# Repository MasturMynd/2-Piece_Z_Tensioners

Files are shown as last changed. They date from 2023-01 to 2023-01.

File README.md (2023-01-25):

# 2-Piece Z Tensioners

Frustrated by a number of cracked stock Z tensioners, I finally decided to take matters into my own hands. The print orientation of the stock Z tensioners puts the most force along the layer lines which can easily result in delamination under normal use. These 2-piece tensioners change the print orientation so the forces being applied are perpendicular to the layer lines, resulting in a stronger part.

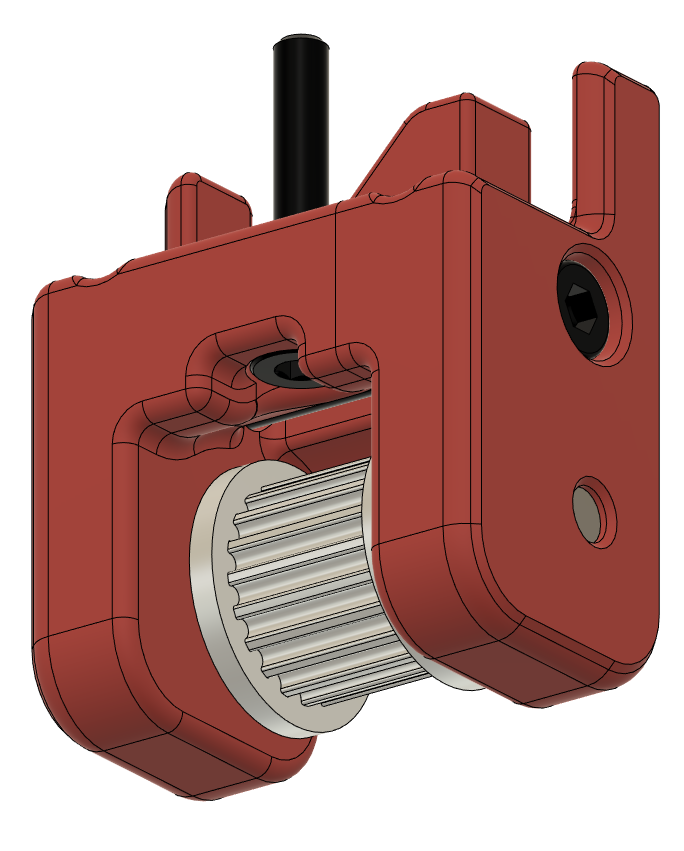
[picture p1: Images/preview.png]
Preview


BOM
---
| Category | Part Description | Qty | Notes |
| --- | --- | --- | --- |
| | M3x25 BHCS | 4 | |
| | M3 Brass heatstake inserts - short M3x5x4 | 4 | |

# Assembly

Before We Begin
---
Make sure that you have the proper parts printed for your setup. If you're using the BOM hardware (M5x30 BHCS) make sure you don't have the internal flange.
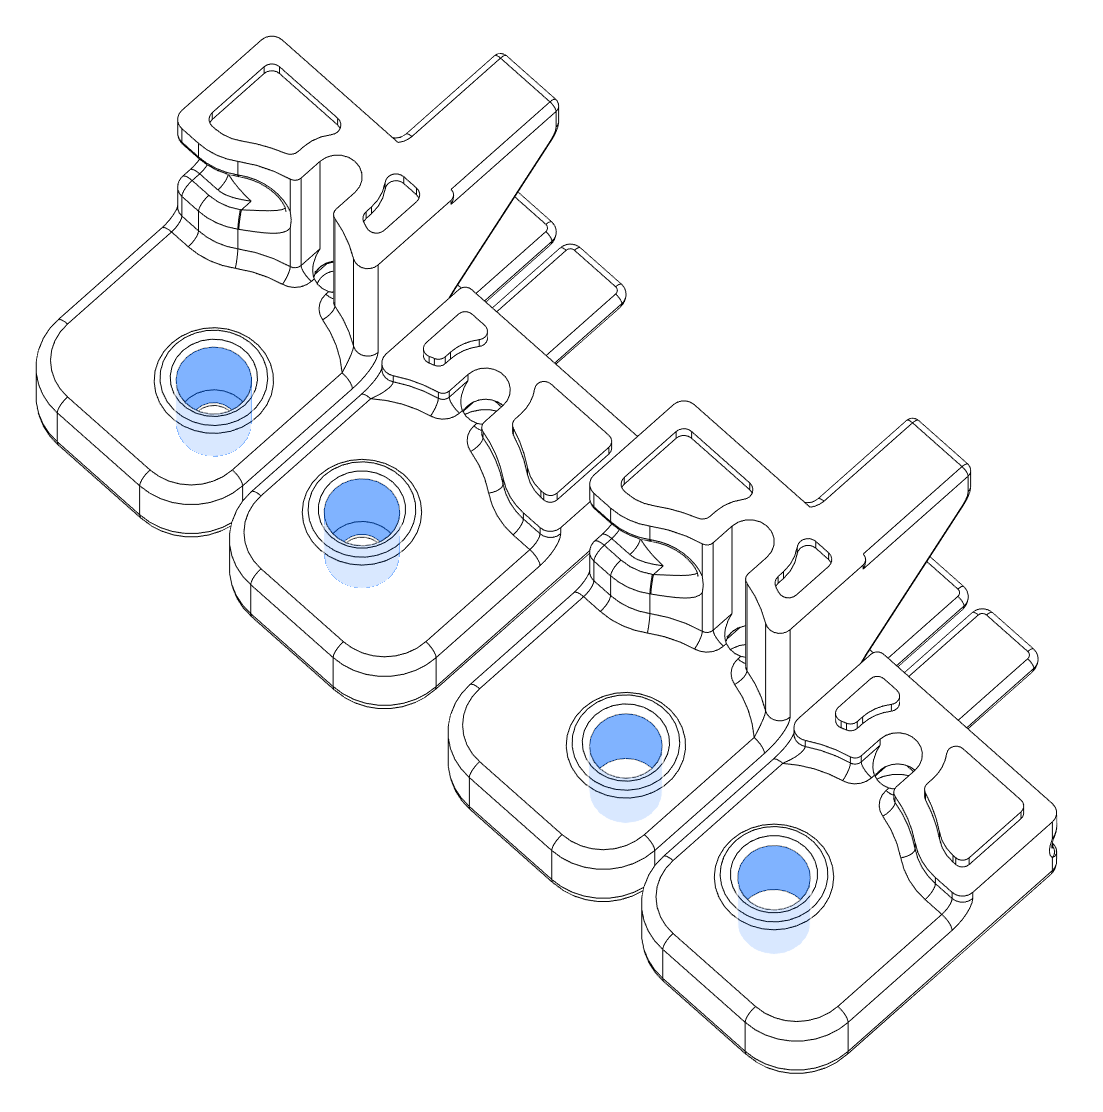
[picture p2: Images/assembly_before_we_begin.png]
Assembly_Before_We_Begin


Heatset Insert
---
Each tensioner assembly requires a single heatset insert that will be used in combination with an M3x25 SHCS to clamp the two pieces together.
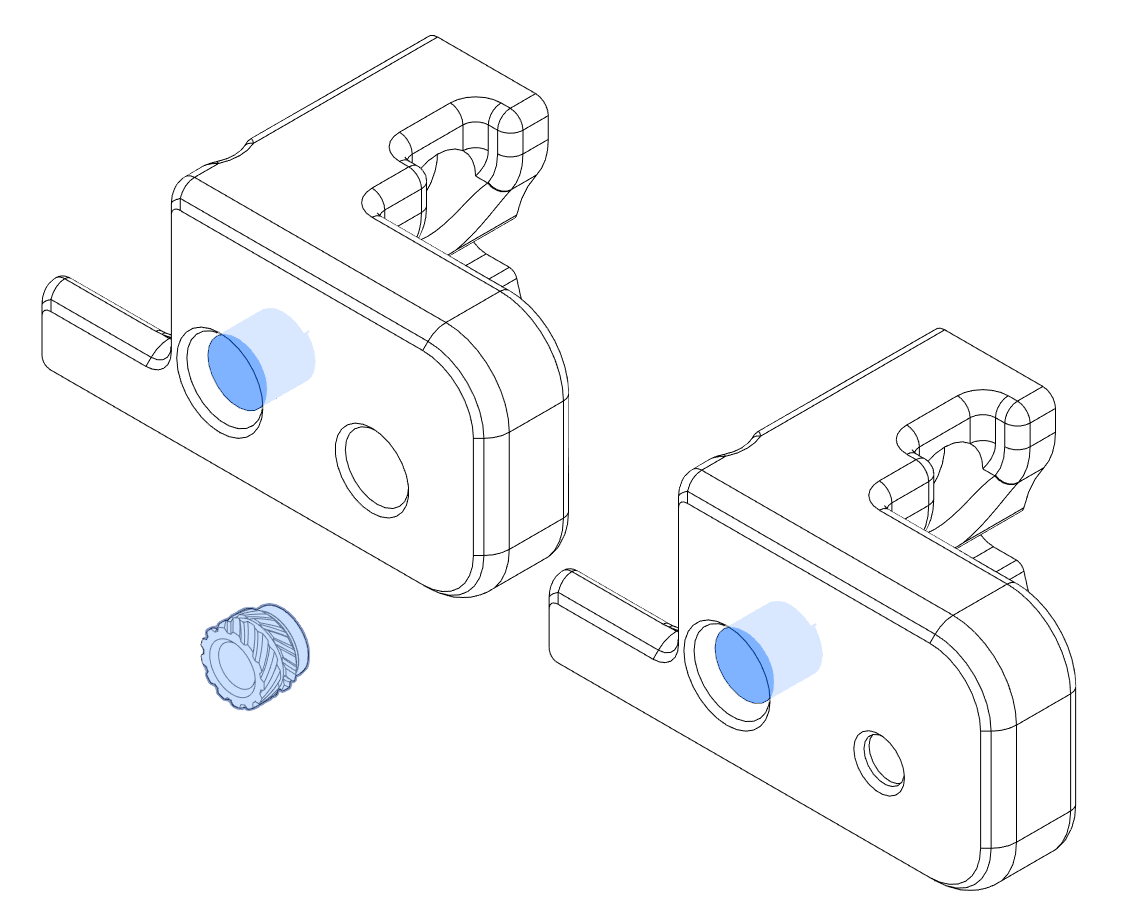
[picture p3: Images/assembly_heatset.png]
Assembly_Heatset


Idler Shaft
---
BOM - Feed the M5x30 BHCS through the from the outside of part 'b' (as outlined in the naming convention)<br />
PIN - Press the 5x28mm pin into the pocket of part 'b' (as outlined in the naming convention)
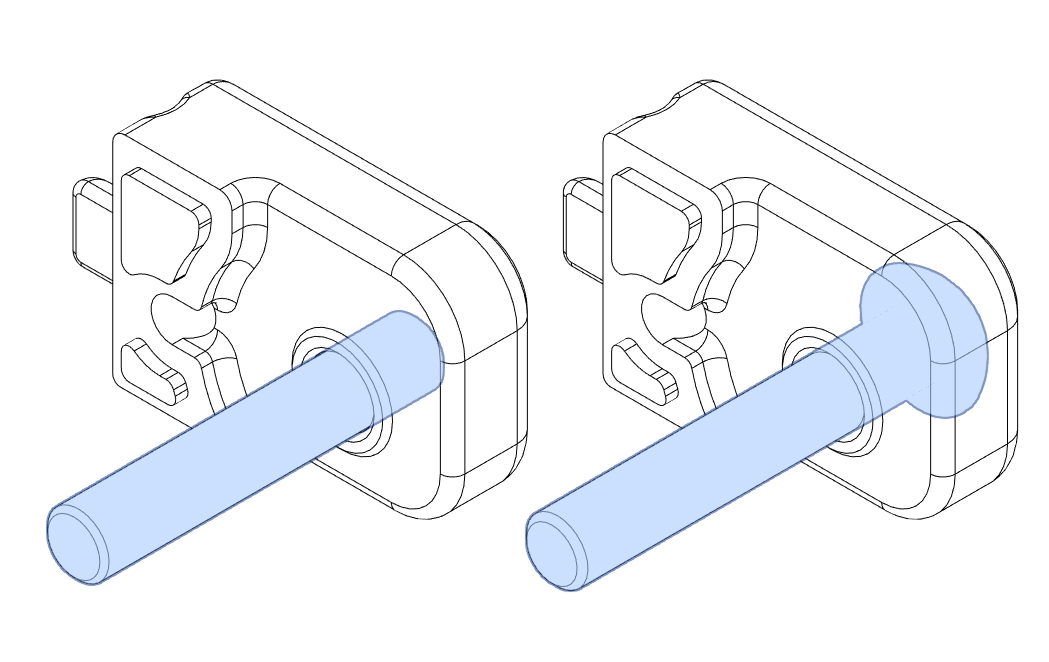
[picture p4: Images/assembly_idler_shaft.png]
Assembly_Idler_Shaft


Idler Installation
---
Push the GT2 20T Idler onto the pin or screw that you installed in the previous step.
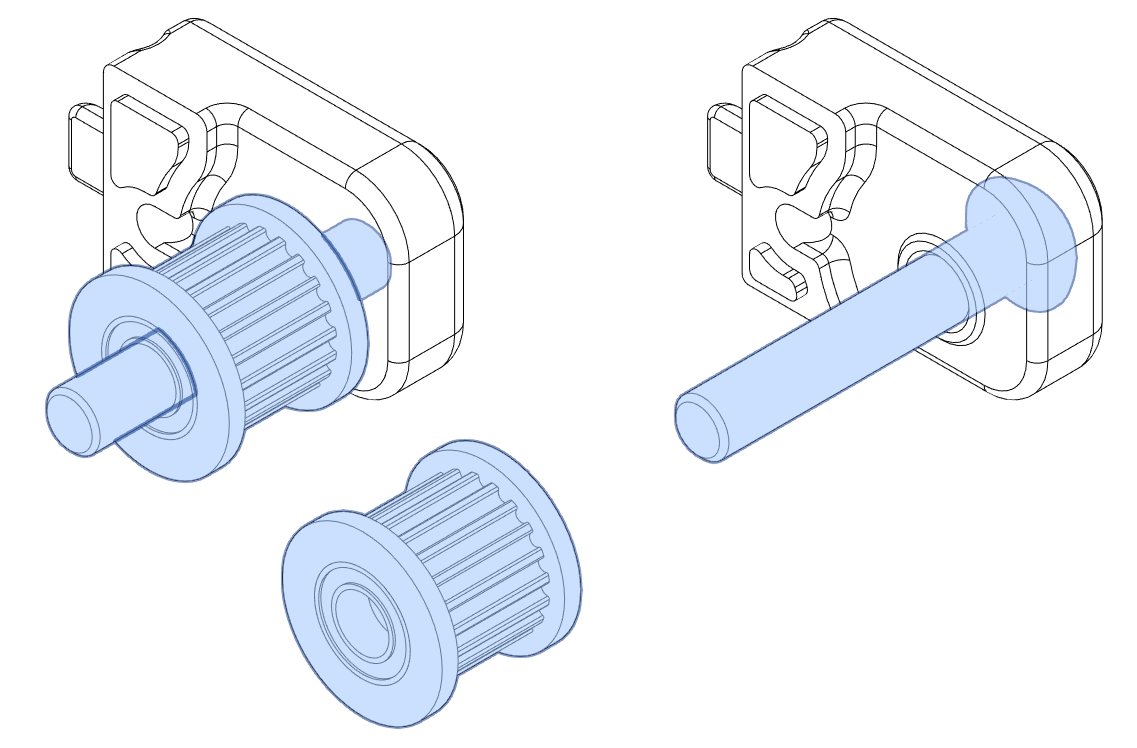
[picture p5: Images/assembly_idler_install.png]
Assembly_Idler_Install


Two Become One
---
Insert the M3x25 SHCS into the hole and use it to clamp the assembly together. For BOM hardware you'll first want to tighten the M5x30 BHCS as the threads have likely butten into plastic and will be harder to turn.
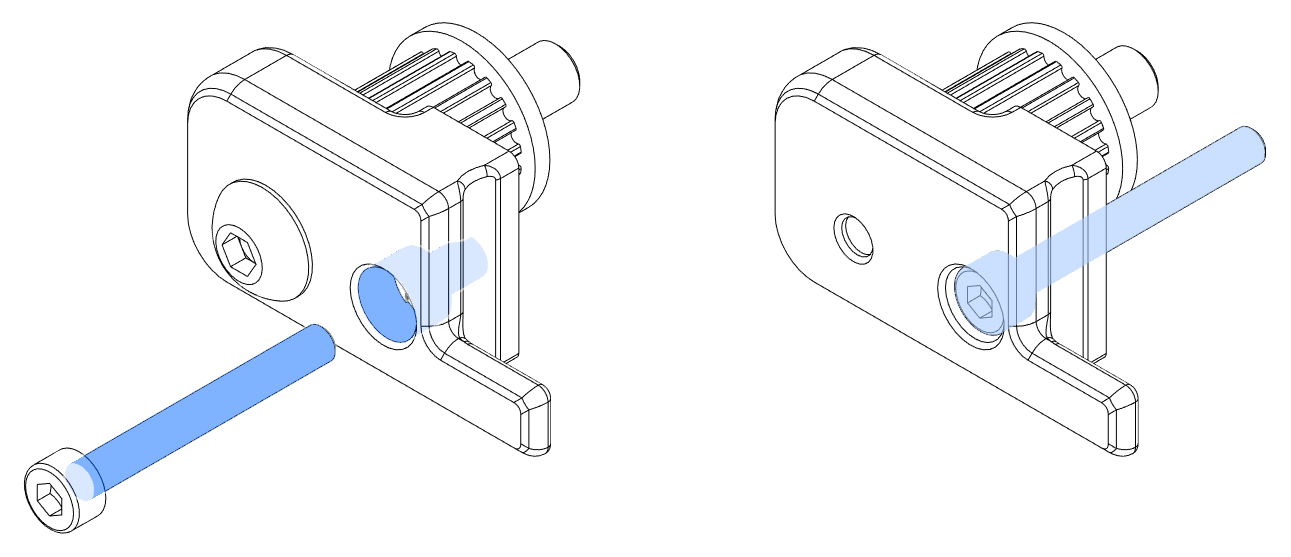
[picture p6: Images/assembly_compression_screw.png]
Assembly_Compression_Screw

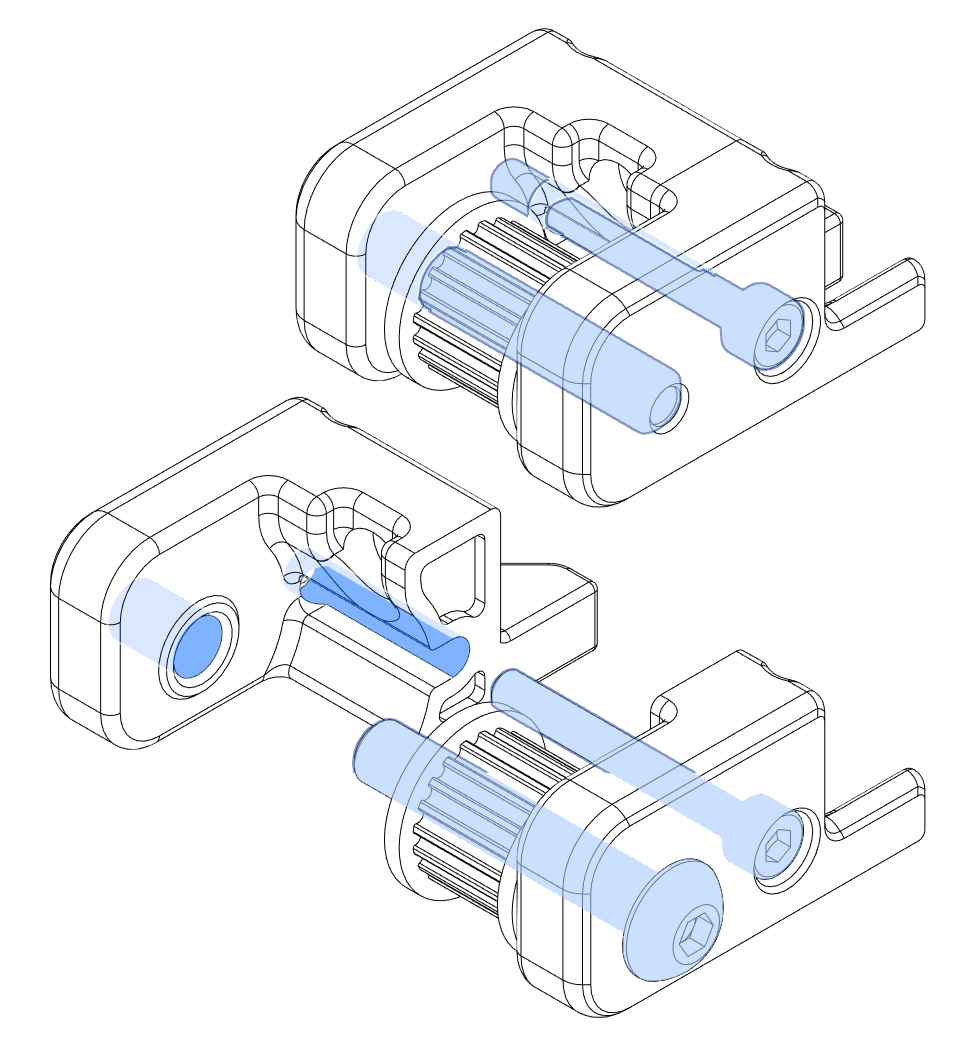
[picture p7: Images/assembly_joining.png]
Assembly_Joining


Tensioning Screw
---
Last, install the M3x16 SHCS that is used to tension the belts against the stock tensioner housings.
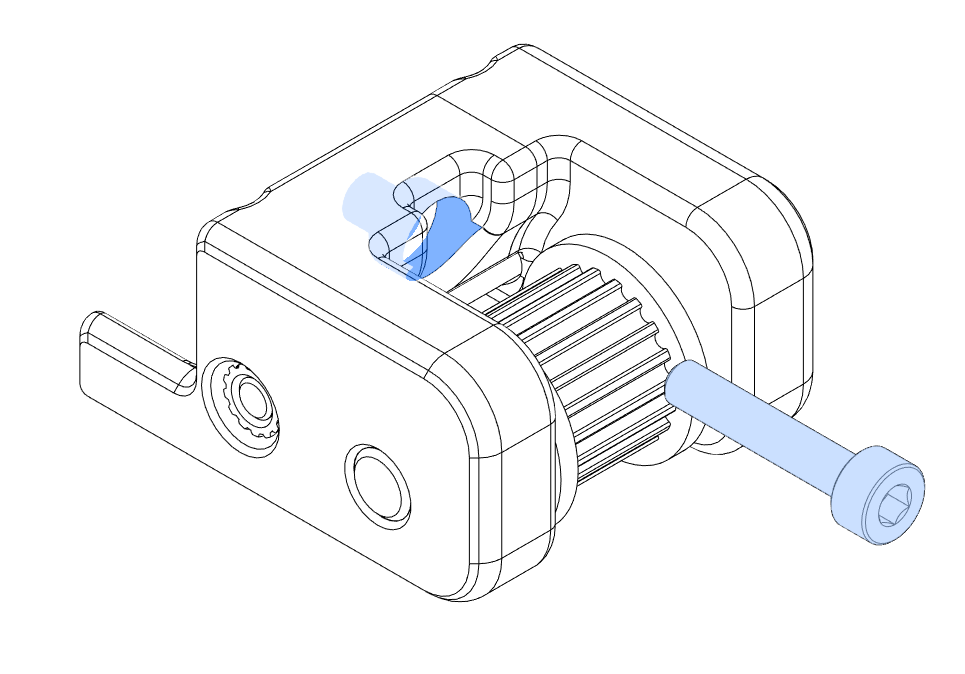
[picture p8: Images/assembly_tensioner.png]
Assembly_Tensioner


Once each of these tensioner assemblies have been completed, you're ready to install in your V2!

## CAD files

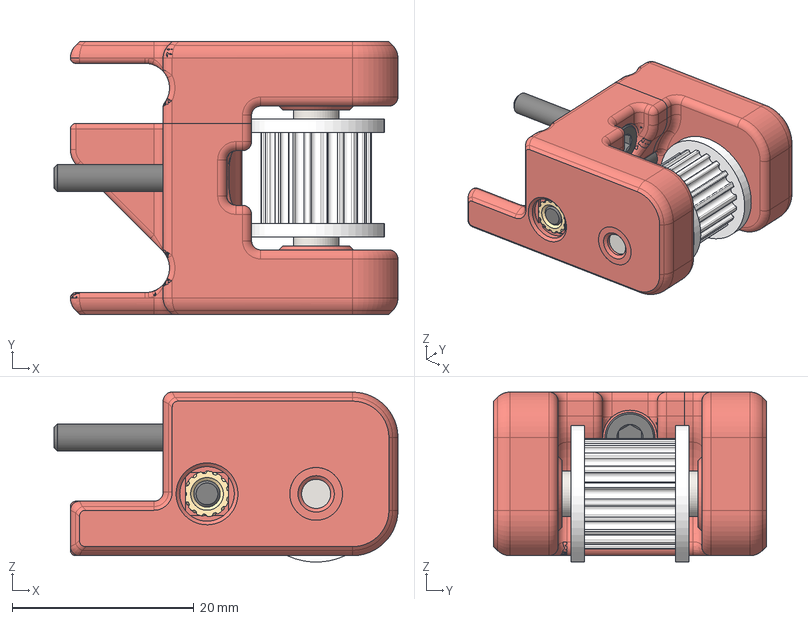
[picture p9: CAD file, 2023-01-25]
CAD/2 Piece Z Idler v4.step
37.8 x 30.0 x 18.7 mm
[a]_z_tensioner_a_9mm_x4
[a]_z_tensioner_b_9mm_x4
M3x16 SHCS v5
M3 Threaded Insert v3
M3x25 SHCS v2
5x28mm Pin
GT2 20T Toothed Idler 9mm
Bearing x 2

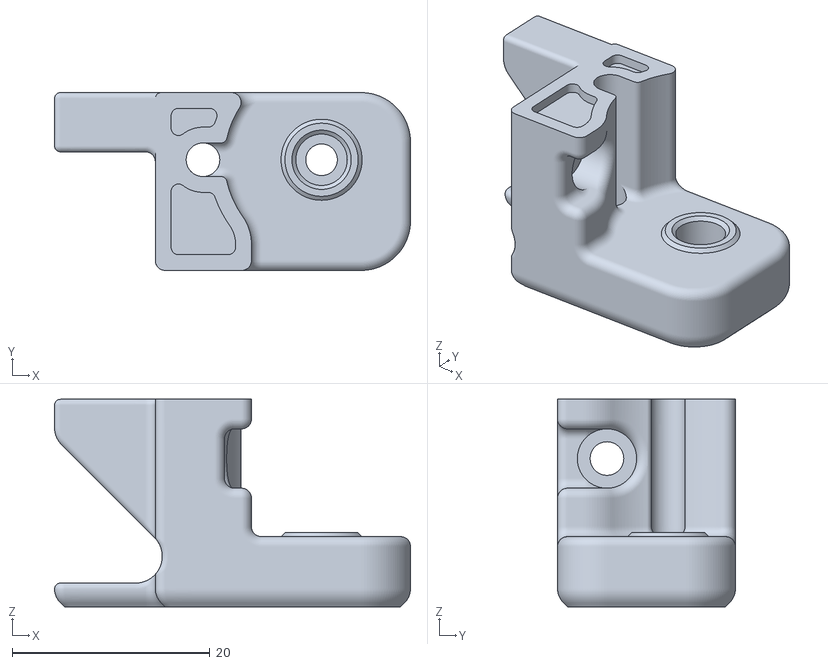
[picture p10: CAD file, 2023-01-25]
STLs/[a]_z_tensioner_a_pinned_9mm_x4.stl
36.0 x 18.0 x 21.0

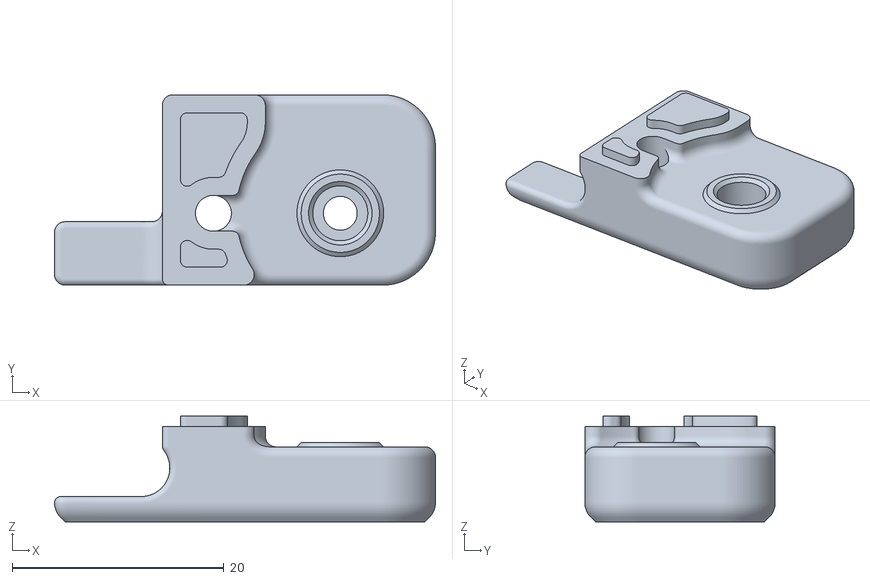
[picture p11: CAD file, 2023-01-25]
STLs/[a]_z_tensioner_b_pinned_9mm_x4.stl
36.0 x 18.0 x 10.0

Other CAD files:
STLs/[a]_z_tensioner_a_9mm_x4.stl
STLs/[a]_z_tensioner_b_9mm_x4.stl

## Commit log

2023-01-25 Corrected Assembly Images
2023-01-25 Replaced Heatset Counterbore with Countersink
    [[a]_z_tensioner_a_9mm_x4.stl, [a]_z_tensioner_a_pinned_9mm_x4.stl]
